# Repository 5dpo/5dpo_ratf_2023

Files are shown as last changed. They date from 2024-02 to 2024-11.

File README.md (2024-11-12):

# 5dpo_ratf_2023

System framework for the Robot@Factory 4.0 competition
([info](https://www.festivalnacionalrobotica.pt/2023/robotfactory-4-0/),
[GitHub](https://github.com/P33a/RobotAtFactory/tree/main)) hosted at the
[Portuguese Robotics Open (FNR)](https://www.festivalnacionalrobotica.pt/).
This framework is the lastest version developed by the
[5dpo Robotics Team](https://5dpo.github.io/) and used in the 2023 edition of
the competition.
Furthermore, the robot is a four-wheeled omnidirectional platform also developed
in the scope of the competition. All the information about the electrical and
mechanical components can be found below.
Finally, the launch file system implemented is bsed on the
[INESC TEC](https://www.inesctec.pt/en) Robotics Navigation Stack that allows
you to have different configurations implemented and selecting just one based on
your environment variables.

## Hardware

- Mechanics (3D files to print are available in [cad](/cad/)):
  - 60mm Aluminum Mecanum Wheels Set (2x left + 2x right, 45° rotational axis)
    ([shop](https://eu.robotshop.com/products/60mm-mecanum-wheel-set-2x-left-2x-right))
  - Metal DC Geared Motor w/Encoder - 12V 251RPM 18Kg.cm (DFRobot)
    ([shop-1](https://eu.robotshop.com/products/12v-dc-motor-251rpm-encoder),
    [shop-2](https://www.dfrobot.com/product-634.html))
- Computing Units:
  - Arduino Mega 2560 Rev3
    ([shop](https://store.arduino.cc/products/arduino-mega-2560-rev3))
  - Raspberry Pi 4B 4GB
    ([shop-1](https://mauser.pt/catalog/product_info.php?products_id=096-7402),
    [shop-2](https://pt.farnell.com/raspberry-pi/rpi4-modbp-4gb/raspberry-pi-4-model-b-4gb/dp/3051887),
    [shop-3](https://pt.mouser.com/ProductDetail/Raspberry-Pi/SC01949?qs=T%252BzbugeAwjjISb%252BwlagpRw%3D%3D),
    [shop-4](https://www.digikey.pt/en/products/detail/raspberry-pi/SC0194-9/10258781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))
- Electronics:
  - DC-DC Buck Converter 300W 6-40V to 1.2-36V 20A Step Dowm
    ([shop](https://www.amazon.com/DIANN-300W-DC-DC-Buck-Converter/dp/B0B4CZ6GRV))
  - Grove Electromagnet
    ([shop](https://eu.robotshop.com/products/grove-electromagnet))
  - LiPo Battery 11.1V 3S
    - Gens ace 5000mAh 11.1V 3S1P 60C Lipo Battery Pack with XT90 Plug Bashing
      Series
      ([shop](https://www.gensace.de/gens-ace-5000mah-11-1v-3s1p-60c-lipo-battery-pack-with-xt-90-plug-bashing-series.html))
    - Tattu 11.1V 15C 3S 10000mAh Lipo Battery Pack
      ([shop](https://www.gensace.de/tattu-11-1v-15c-3s-10000mah-lipo-battery-pack.html))
  - Micro Switch with Roller Lever Arm
    ([shop](https://mauser.pt/catalog/product_info.php?products_id=010-1473))
  - Power ON/OFF Switch
    ([shop](https://mauser.pt/catalog/product_info.php?products_id=010-0626))
- Sensors:
  - 10 DoF Inertial Measurement Unit (IMU)
    ([shop](https://www.waveshare.com/10-dof-imu-sensor-b.htm))
  - Raspberry Pi Camera Board v2.1 (8MP, 1080p)
    ([shop-1](https://mauser.pt/catalog/product_info.php?products_id=096-4061),
    [shop-2](https://pt.farnell.com/raspberry-pi/rpi-8mp-camera-board/raspberry-pi-camera-board-v2/dp/2510728),
    [shop-3](https://pt.mouser.com/ProductDetail/Raspberry-Pi/SC0023?qs=T%252BzbugeAwjgRU4vb4%252BbLIg%3D%3D),
    [shop-4](https://www.digikey.pt/en/products/detail/raspberry-pi/SC0023/6152810?s=N4IgTCBcDaIIwDYCcAGAtHFc5oHIBEQBdAXyA))
  - YDLIDAR X4 360° Laser Scanner
    ([shop](https://eu.robotshop.com/products/ydlidar-x4-360-laser-scanner))

## Firmware

- Arduino Mega 2560 Rev3 ([doc](https://docs.arduino.cc/hardware/mega-2560/))
- PlatformIO ([url](https://platformio.org/),
  [vscode](https://marketplace.visualstudio.com/items?itemName=platformio.platformio-ide),
  [clion](https://plugins.jetbrains.com/plugin/13922-platformio-for-clion))
  - Pre-requisite:
    ```sh
    sudo apt install python3-venv
    ```
  - Setup udev rules
    ([source](https://docs.platformio.org/en/stable/core/installation/udev-rules.html)):
    ```sh
    curl -fsSL https://raw.githubusercontent.com/platformio/platformio-core/develop/platformio/assets/system/99-platformio-udev.rules | sudo tee /etc/udev/rules.d/99-platformio-udev.rules

    sudo service udev restart
    sudo usermod -a -G dialout $USER
    sudo usermod -a -G plugdev $USER
    ```
  - If you want to define a fixed name to the serial port connection, add the
    following lines to a file `/etc/udev/rules.d/99-usb-serial.rule`
    ([source](https://roboticsknowledgebase.com/wiki/tools/udev-rules/)):
    ```conf
    SUBSYSTEM=="tty", ATTRS{idVendor}=="2341", ATTRS{idProduct}=="0042", SYMLINK+="ttyArduinoMega"
    ```
    - _Note:_ this approach creates a symbolic link, but the original device
      still appears in the `/dev/` folder
- Implementation: [5dpo_ratf_firmware](/firmware/5dpo_ratf_firmware/)

## ROS

**Current version**
- [Ubuntu 20.04.5 LTS](https://releases.ubuntu.com/focal/)
- [ROS Noetic](https://wiki.ros.org/noetic)

**Nodes**
- Drivers:
  - [sdpo_ratf_ros_driver](/drivers/5dpo_ratf_ros_driver/) (driver to
    communicate to the firmware running in the Arduino Mega 2560)
  - [sdpo_driver_omnijoy](/drivers/5dpo_driver_omnijoy/) (joystick driver
    compatible with omnidirectional platforms)
  - [sdpo_driver_laser_2d](/drivers/5dpo_driver_laser_2d/) (driver to
    communicate through a serial connection with the YDLIDAR X4)
  - [sdpo_driver_ros_camera](/drivers/5dpo_driver_ros_camera/) (camera driver
    to publish the poses of ArUco markers) _(NOT STABLE!)_
- Localization:
  - [sdpo_ros_odom](/localization/5dpo_ros_odom/) (wheeled odometry relative
    pose estimation)
  - [sdpo_ratf_ros_localization](/localization/5dpo_ratf_ros_localization/)
    (beacon-based Extended Kalman Filter to estimate the pose of the robot)
- Navigation:
  - [sdpo_ratf_ros_path_planning](/navigation/5dpo_ratf_ros_path_planning/)
    (trajectory controller and path planning to execute the competition rounds)
- Navigation Configuration:
  - [sdpo_ratf_ros_nav_conf](/5dpo_ratf_ros_nav_conf/) (launch file system)

## Usage

### Configurations

- `basic`
  - Drivers
    - [sdpo_ratf_ros_driver](/drivers/5dpo_ratf_ros_driver/)
    - [sdpo_driver_omnijoy](/drivers/5dpo_driver_omnijoy/)
  - Human-Machine Interface (HMI)
    - rviz
  - Localization
    - [sdpo_ros_odom](/localization/5dpo_ros_odom/)
- `ratf2023`
  - Drivers
    - [sdpo_ratf_ros_driver](/drivers/5dpo_ratf_ros_driver/)
    - [sdpo_driver_omnijoy](/drivers/5dpo_driver_omnijoy/)
    - [sdpo_driver_laser_2d](/drivers/5dpo_driver_laser_2d/)
  - Human-Machine Interface (HMI)
    - rviz
  - Localization
    - [sdpo_ros_odom](/localization/5dpo_ros_odom/)
    - [sdpo_ratf_ros_localization](/localization/5dpo_ratf_ros_localization/)
  - Navigation
    - [sdpo_ratf_ros_path_planning](/navigation/5dpo_ratf_ros_path_planning/)
- `ratf2023_imu_test` **(specific to Raspberry Pi!)**
  - Drivers
    - [imu_filter_madgwick](/drivers/imu_tools/imu_filter_madgwick/)
    - [MPU9255_node](/drivers/MPU9255_for_5dpo/)
    - [sdpo_ratf_ros_driver](/drivers/5dpo_ratf_ros_driver/)
    - [sdpo_driver_omnijoy](/drivers/5dpo_driver_omnijoy/)
    - [sdpo_driver_laser_2d](/drivers/5dpo_driver_laser_2d/)
  - Human-Machine Interface (HMI)
    - rviz
  - Localization
    - [robot_pose_ekf](/localization/robot_pose_ekf/)
    - [sdpo_ros_odom](/localization/5dpo_ros_odom/)
    - [sdpo_ratf_ros_localization](/localization/5dpo_ratf_ros_localization/)
  - Navigation
    - [sdpo_ratf_ros_path_planning](/navigation/5dpo_ratf_ros_path_planning/)
  - You may need to either clone the source of additional dependencies or
    installing the following nodes:
    ```sh
    sudo apt install ros-noetic-robot-pose-ekf
    sudo apt install ros-noetic-imu-complementary-filter
    ```
    - **Note:** if you do not want to use the IMU, please add a `CATKIN_IGNORE`
      file inside each of the IMU-specific nodes. Also, given that the MPU node
      requires a specific library of Raspberry Pi for communication with the
      IMU, the code will not compile in your x86 system.

**Usage**

```sh
# Robot id
export ROBOT_ID=<id>                # (default: unnamed_robot)
# Configuration
export ROBOT_CONF=<configuration>   # (default: basic)
```

If you want to set up a persistent `ROBOT_ID` environment variable, add the
following line to the file `/etc/environment`:

```sh
ROBOT_ID=<id>
```

### Build

```sh
mkdir ~/ros1_ws/src -p
cd ~/ros1_ws/src

git clone git@github.com:5dpo/5dpo_ratf_2023.git

cd ../
catkin_make --force-cmake -DCMAKE_BUILD_TYPE=Release
```

### Launch

```sh
export ROBOT_CONF=<basic|ratf2023>
roslaunch sdpo_ratf_ros_nav_conf wake_up_almighty_ratf.launch
```

## License

Distributed under the _MIT License_.
See [LICENSE](/LICENSE) for more information.

## References
If using this code for research purposes, please cite:
```bash
@INPROCEEDINGS{5dpoRAF,
  author={Sousa, Ricardo B. and Rocha, Cláudia D. and Martins, João G. and Pedro Costa, João and Padrão, João Tomás and Sarmento, José Maria and Carvalho, José Pedro and Lopes, Maria S. and Costa, Paulo G. and Moreira, António Paulo},
  booktitle={2024 IEEE International Conference on Autonomous Robot Systems and Competitions (ICARSC)}, 
  title={A Robotic Framework for the Robot@Factory 4.0 Competition}, 
  year={2024},
  volume={},
  number={},
  pages={66-73},
  doi={10.1109/ICARSC61747.2024.10535935}}
```

## Contacts

- António Paulo Moreira ([github](https://github.com/apaulomoreira),
  [mail](mailto:amoreira@fe.up.pt))
- Cláudia Daniela Rocha ([github](https://github.com/rochaclaudia),
  [mail](mailto:claudia.d.rocha@inesctec.pt))
- João G. Martins ([github](https://github.com/Joao-G-Martins),
  [mail:student](mailto:up201806222@edu.fe.up.pt),
  [mail:inesctec](mailto:joao.g.martins@inesctec.pt))
- João Pedro Costa ([github](https://github.com/costajoao1641),
  [mail](mailto:up201806431@edu.fe.up.pt))
- João Tomás Padrão ([github](https://github.com/JoaoP4dr4o),
  [mail](mailto:up202108766@edu.fe.up.pt))
- José Maria Sarmento ([github](https://github.com/JoseMQS),
  [mail](mailto:jose.m.sarmento@inesctec.pt))
- José Pedro Carvalho ([github](https://github.com/Jose-PCarvalho),
  [mail](mailto:jpcarvalho@fe.up.pt))
- Maria Silva Lopes ([github](https://github.com/mariaslopes),
  [mail:student](mailto:up201806775@edu.fe.up.pt),
  [mail:inesctec](mailto:maria.s.lopes@inesctec.pt))
- Paulo José Gomes da Costa ([github](https://github.com/P33a),
  [mail](mailto:paco@fe.up.pt))
- Ricardo B. Sousa ([github](https://github.com/sousarbarb/),
  [gitlab](https://gitlab.inesctec.pt/ricardo.b.sousa),
  [mail:inesctec](mailto:ricardo.b.sousa@inesctec.pt),
  [mail:personal](mailto:sousa.ricardob@outlook.com),
  [mail:student](mailto:up201503004@edu.fe.up.pt))

Project Link:
https://github.com/5dpo/5dpo_ratf_2023/.

## Acknowledgements

- [Faculty of Engineering, University of Porto (FEUP)](https://sigarra.up.pt/feup/en/)
- [Electrical and Computers Engineering Department (DEEC) @ FEUP](https://sigarra.up.pt/feup/en/UNI_GERAL.UNIDADE_VIEW?pv_unidade=13)
- [CRIIS - Centre for Robotics in Industry and Intelligent Systems](https://www.inesctec.pt/en/centres/criis/) from
  [INESC TEC - Institute for Systems and Computer Engineering, Technology and Science](https://www.inesctec.pt/en/)

## Funding

TBC.

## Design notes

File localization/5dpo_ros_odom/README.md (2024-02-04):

# [5dpo_ros_odom](https://github.com/5dpo/5dpo_ros_odom)

This repository implements a data processor for the estimation of the robot pose
based on odometric-only data (e.g., wheeled, laser, visual, and/or inertial
odometry). The ROS package implemented in this repository makes available nodes
that may leverage one and/or multiple sources of odometry data for dead
reckoning pose estimation of the robot.

**Version 1.4.0**

**With this version, it is possible to do:**

- Wheeled odometry (four-wheeled omnidirectional steering geometry)
- Wheeled odometry (differential and three-wheeled omnidirectional steering
  geometries)
- Inverse wheeled odometry
- Enable/disable publication of the tf base_frame_id > odom_frame_id
- Limit the maximum angular speed of the wheels and scale the velocities

**The next version will add these features:**

- Wheeled odometry (tricycle steering geometry)
- Fusion of wheels and inertial odometry data

## ROS

**Current version:**

- [Ubuntu 20.04.5 LTS](https://releases.ubuntu.com/focal/)
- [ROS Noetic](https://wiki.ros.org/noetic)

### Dependencies

- [roscpp](https://wiki.ros.org/roscpp)
- [geometry_msgs](https://wiki.ros.org/geometry_msgs)
- [nav_msgs](https://wiki.ros.org/nav_msgs)
- [sdpo_ros_interfaces_hw](https://github.com/5dpo/5dpo_ros_interfaces)
- [tf](https://wiki.ros.org/tf)

### Parameters

- base_frame_id (`std::string = "base_footprint"`): tf frame id of the robot
  base footprint coordinate frame
- odom_frame_id (`std::string = "odom"`): tf frame id of the robot odometry
  coordinate frame
- publish_tf (`bool = true`): enable the publication of the tf
  base_frame_id > odom_frame_id
- steering_geometry: steering geometry of the mobile robot
  (`"diff" | "tricyc" | "omni3" | "omni4"`)
  - w_ref_max_enabled (`bool = false`): enable a maximum angular speed for the
    robot wheels
  - w_ref_max (`double`): maximum angular speed of the robot wheels
  - Differential drive
    - rob_dist_between_wh (`double`): distance between left-right wheels (m)
    - wh_right_diam (`double`): right wheel diameter (m)
    - wh_right_idx (`size_t`): right wheel index in the
      [mot_enc_array.msg](https://github.com/5dpo/5dpo_ros_interfaces/blob/main/5dpo_ros_interfaces_hw/msg/mot_enc_array.msg)
      (0..1)
    - wh_right_inv (`bool`): invert positive direction of the right
      wheel angular motion
    - wh_left_diam (`double`): left wheel diameter (m)
    - wh_left_idx (`size_t`): left wheel index in the
      [mot_enc_array.msg](https://github.com/5dpo/5dpo_ros_interfaces/blob/main/5dpo_ros_interfaces_hw/msg/mot_enc_array.msg)
      (0..1)
    - wh_left_inv (`bool`): invert positive direction of the left
      wheel angular motion
  - Tricycle
    - TBD 
  - Three-wheeled omnidirectional robot
    - rob_dist_center_wh (`double`): distance between the robot geometric center
      and the omnidirectional wheels (m)
    - wh_front_right_diam (`double`): front-right wheel diameter (m)
    - wh_front_right_idx (`size_t`): front-right wheel index in the
      [mot_enc_array.msg](https://github.com/5dpo/5dpo_ros_interfaces/blob/main/5dpo_ros_interfaces_hw/msg/mot_enc_array.msg)
      (0..2)
    - wh_front_right_inv (`bool`): invert positive direction of the front-right
      wheel angular motion
    - wh_front_left_diam (`double`): front-left wheel diameter (m)
    - wh_front_left_idx (`size_t`): front-left wheel index in the
      [mot_enc_array.msg](https://github.com/5dpo/5dpo_ros_interfaces/blob/main/5dpo_ros_interfaces_hw/msg/mot_enc_array.msg)
      (0..2)
    - wh_front_left_inv (`bool`): invert positive direction of the front-left
      wheel angular motion
    - wh_back_diam (`double`): back wheel diameter (m)
    - wh_back_idx (`size_t`): back wheel index in the
      [mot_enc_array.msg](https://github.com/5dpo/5dpo_ros_interfaces/blob/main/5dpo_ros_interfaces_hw/msg/mot_enc_array.msg)
      (0..2)
    - wh_back_inv (`bool`): invert positive direction of the back
      wheel angular motion
  - Four-wheeled omnidirectional robot
    - rob_dist_between_front_back_wh (`double`): distance between front-back
      wheels (m)
    - rob_dist_between_left_right_wh (`double`): distance between left-right
      wheels (m)
    - wh_front_left_diam (`double`): front-left wheel diameter (m)
    - wh_front_left_idx (`size_t`): front-left wheel index in the
      [mot_enc_array.msg](https://github.com/5dpo/5dpo_ros_interfaces/blob/main/5dpo_ros_interfaces_hw/msg/mot_enc_array.msg)
      (0..3)
    - wh_front_left_inv (`bool`): invert positive direction of the front-left
      wheel angular motion
    - wh_front_right_diam (`double`): front-right wheel diameter (m)
    - wh_front_right_idx (`size_t`): front-right wheel index in the
      [mot_enc_array.msg](https://github.com/5dpo/5dpo_ros_interfaces/blob/main/5dpo_ros_interfaces_hw/msg/mot_enc_array.msg)
      (0..3)
    - wh_front_right_inv (`bool`): invert positive direction of the front-right
      wheel angular motion
    - wh_back_left_diam (`double`): back-left wheel diameter (m)
    - wh_back_left_idx (`size_t`): back-left wheel index in the
      [mot_enc_array.msg](https://github.com/5dpo/5dpo_ros_interfaces/blob/main/5dpo_ros_interfaces_hw/msg/mot_enc_array.msg)
      (0..3)
    - wh_back_left_inv (`bool`): invert positive direction of the back-left
      wheel angular motion
    - wh_back_right_diam (`double`): back-right wheel diameter (m)
    - wh_back_right_idx (`size_t`): back-right wheel index in the
      [mot_enc_array.msg](https://github.com/5dpo/5dpo_ros_interfaces/blob/main/5dpo_ros_interfaces_hw/msg/mot_enc_array.msg)
      (0..3)
    - wh_back_right_inv (`bool`): invert positive direction of the back-right
      wheel angular motion

### Subscribes

- cmd_vel
  ([Twist.msg](https://docs.ros.org/en/noetic/api/geometry_msgs/html/msg/Twist.html))

**sdpo_ros_odom_wh**

- motors_encoders
  ([mot_enc_array.msg](https://github.com/5dpo/5dpo_ros_interfaces/blob/main/5dpo_ros_interfaces_hw/msg/mot_enc_array.msg))

### Publishes

- cmd_vel_ref
  ([Twist.msg](https://docs.ros.org/en/noetic/api/geometry_msgs/html/msg/Twist.html))
- motors_ref
  ([mot_ref.msg](https://github.com/5dpo/5dpo_ros_interfaces/blob/main/5dpo_ros_interfaces_hw/msg/mot_ref.msg))
- odom
  ([Odometry.msg](https://docs.ros.org/en/noetic/api/nav_msgs/html/msg/Odometry.html))
- tf (N/A)
  - base_frame_id > odom_frame_id

### Services

None.

### Actions

None.

## Usage

### Build

```sh
# Create catkin workspace
mkdir -p ~/catkin_ws/src

# Clone repository
cd ~/catkin_ws/src
git clone git@github.com:5dpo/5dpo_ros_odom.git

# Build
cd ..
catkin build
# OR catkin_make_isolated (more slow, build and check dependencies individually)
# OR catkin build (requires catkin tools)
```

### Launch

**sdpo_ros_odom_wh**

```sh
roslaunch sdpo_ros_odom sdpo_ros_odom_wh.launch
```

## Contacts

If you have any questions or you want to know more about this work, please
contact one of the contributors of this package:

- Héber Miguel Sobreira ([github](https://github.com/HeberSobreira),
  [gitlab](https://gitlab.inesctec.pt/heber.m.sobreira),
  [mail](mailto:heber.m.sobreira@inesctec.pt))
- Ricardo B. Sousa ([github](https://github.com/sousarbarb/),
  [gitlab](https://gitlab.inesctec.pt/ricardo.b.sousa),
  [mail:inesctec](mailto:ricardo.b.sousa@inesctec.pt),
  [mail:personal](mailto:sousa.ricardob@outlook.com),
  [mail:professor](mailto:rbs@fe.up.pt),
  [mail:student](mailto:up201503004@edu.fe.up.pt))

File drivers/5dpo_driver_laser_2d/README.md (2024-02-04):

# [5dpo_driver_laser_2d](https://github.com/5dpo/5dpo_driver_laser_2d)

This repository focus on developing a driver for communicating with
[RPLIDAR](https://www.slamtec.com/en) and variants (specifically,
[YDLIDAR](https://www.ydlidar.com/)) of 2D laser scanners.
The main purpose is to be able to compensate in the future the linear and
angular velocity in the laser data.

**Version 2.4.0**

**With this version, it is possible to do:**

- [YDLIDAR X4](https://www.ydlidar.com/products/view/5.html) support
- [RPLIDAR S2](https://www.slamtec.com/en/S2) support
- tf publication of the laser pose relative to the robot's coordinate frame
- Library available to use the lasers outside of this ROS package
- Dynamic reconfiguration of the laser pose relative to the base footprint
  coordinate frame

**The next version will add these features:**

- [RPLIDAR S2](https://www.slamtec.com/en/S2) dense mode

## ROS

**Current version:**

- [Ubuntu 20.04.5 LTS](https://releases.ubuntu.com/focal/)
- [ROS Noetic](https://wiki.ros.org/noetic)

### Dependencies

- [roscpp](https://wiki.ros.org/roscpp)
- [rospy](https://wiki.ros.org/rospy)
- [dynamic_reconfigure](https://wiki.ros.org/dynamic_reconfigure)
- [sdpo_ros_serial_port](https://github.com/5dpo/5dpo_ros_serial_port)
- [sensor_msgs](https://wiki.ros.org/sensor_msgs)
- [tf](https://wiki.ros.org/tf)

### Parameters

- model (`std::string`): model of the 2D laser (`"rplidars2" | "ydlidarx4"`)
- serial_port_name (`std::string = "/dev/ttyUSB0"`): name of the serial port
  - **Note:** do not forget to execute the following commands in the terminal:
    ```shell
    # Add user to group
    sudo usermod -a -G dialout $USER
    sudo usermod -a -G plugdev $USER

    # Update permissions of the serial port (a - all users + rw - read&write)
    sudo chmod a+rw /dev/ttyUSB0
    ```
- baud_rate (`unsigned int`): baud rate of the serial connection (bps)
  - [YDLIDAR X4](https://www.ydlidar.com/products/view/5.html): `115200`
  - [RPLIDAR S2](https://www.slamtec.com/en/S2): `1000000`
- base_frame_id (`std::string = "base_footprint"`): tf frame id of the robot
  base footprint coordinate frame
- laser_frame_id (`std::string = "laser"`): tf frame id of the 2D laser scanner
  coordinate frame
- laser_pose_x (`float = 0.0`): x of the laser pose relative to the robot base
  footprint coordinate frame (m)
- laser_pose_y (`float = 0.0`): y of the laser pose relative to the robot base
  footprint coordinate frame (m)
- laser_pose_z (`float = 0.0`): z of the laser pose relative to the robot base
  footprint coordinate frame (m)
- laser_pose_yaw (`float = 0.0`): yaw angle of the laser pose relative to the
  robot base footprint coordinate frame (deg)
- laser_pose_pitch (`float = 0.0`): pitch angle of the laser pose relative to
  the robot base footprint coordinate frame (deg)
- laser_pose_roll (`float = 0.0`): roll angle of the laser pose relative to the
  robot base footprint coordinate frame (deg)
- dist_min (`float`): minimum distance range (m)
- dist_max (`float`): maximum distance range (m)
- angle_min (`float`): minimum angle range (deg, `[-180.0, 180.0[`)
- angle_max (`float`): maximum angle range (deg, `[-180.0, 180.0[`)
  - **Note:** if a minimum or a maximum value is set, both limits must be
    defined!

### Subscribes

None.

### Publishes

- laser_scan_point_cloud
  ([PointCloud.msg](https://docs.ros.org/en/api/sensor_msgs/html/msg/PointCloud.html))
- tf (N/A)
  - laser_frame_id > base_frame_id

### Services

None.

### Actions

None.

## Usage

### Build

```sh
# Create catkin workspace
mkdir -p ~/catkin_ws/src

# Clone repository
cd ~/catkin_ws/src
git clone git@github.com:5dpo/5dpo_driver_laser_2d.git

# Build
cd ..
catkin build
# OR catkin_make_isolated (more slow, build and check dependencies individually)
# OR catkin build (requires catkin tools)
```

### Launch

**[YDLIDAR X4](https://www.ydlidar.com/products/view/5.html)**

```sh
roslaunch sdpo_driver_laser_2d sdpo_driver_laser_2d_YDLIDARX4.launch
```

**[RPLIDAR S2](https://www.slamtec.com/en/S2)**

```sh
roslaunch sdpo_driver_laser_2d sdpo_driver_laser_2d_RPLIDARS2.launch
```

## Contacts

If you have any questions or you want to know more about this work, please
contact one of the contributors of this package:

- Héber Miguel Sobreira ([github](https://github.com/HeberSobreira),
  [gitlab](https://gitlab.inesctec.pt/heber.m.sobreira),
  [mail](mailto:heber.m.sobreira@inesctec.pt))
- Ricardo B. Sousa ([github](https://github.com/sousarbarb/),
  [gitlab](https://gitlab.inesctec.pt/ricardo.b.sousa),
  [mail:inesctec](mailto:ricardo.b.sousa@inesctec.pt),
  [mail:personal](mailto:sousa.ricardob@outlook.com),
  [mail:professor](mailto:rbs@fe.up.pt),
  [mail:student](mailto:up201503004@edu.fe.up.pt))

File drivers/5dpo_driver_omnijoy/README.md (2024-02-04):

# 5dpo_driver_omnijoy

**Version 0.0.0**

This repository implements a ROS driver to control an omnidirectional robot
(but also compatible with other steering geometries) with a joystick controller.

**With this version, it is possible to do:**

- Joystick control of a mobile robot

**The next version will add these features:**

- No further development is foreseen for this package

## ROS

**Current version:**

- [Ubuntu 20.04.5 LTS](https://releases.ubuntu.com/focal/)
- [ROS Noetic](https://wiki.ros.org/noetic)

### Dependencies

- [roscpp](https://wiki.ros.org/roscpp)
- [geometry_msgs](https://wiki.ros.org/geometry_msgs)
- [joy](https://wiki.ros.org/joy)

### Parameters

- axis_linear_x (`int = 1`): index number of x linear axis (`/joy.axes`)
- axis_linear_y (`int = 2`): index number of y linear axis (`/joy.axes`)
- axis_angular (`int = 0`): index number of angular linear axis (`/joy.axes`)
- axis_deadman (`int = 4`): index number of button for deadman switch
  (`/joy.buttons`)
- axis_turbo (`int = 5`): index number of button for turbo (`/joy.buttons`)
- axis_turbo_up (`int = 6`): index number of button for increasing boost
  (`/joy.buttons`)
- axis_turbo_down (`int = 7`): index number of button for decreasing boost
  (`/joy.buttons`)
- scale_angular (`double = 0.2`): angular scale to normalize
  [`Joy.msg`](https://docs.ros.org/en/melodic/api/sensor_msgs/html/msg/Joy.html)
- scale_linear (`double = 0.1`): linear scale to normalize
  [`Joy.msg`](https://docs.ros.org/en/melodic/api/sensor_msgs/html/msg/Joy.html)
- turbo_scale_linear (`double = 0.2`): use this scale instead of `scale_linear`
  when pressing the turbo button
- turbo_max_scale_linear (`double = 0.4`): maximum turbo scale
- turbo_scale_angular (`double = 0.4`): use this scale instead of
  `scale_angular` when pressing the turbo button

In order to know the index numbers of your controller, go to
[joy](https://wiki.ros.org/joy) documentation, _5. Application_, to see the
options available for those parameters.

### Subscribes

- joy
([`Joy.msg`](https://docs.ros.org/en/melodic/api/sensor_msgs/html/msg/Joy.html))

### Publishes

- cmd_vel
  ([`Twist.msg`](https://docs.ros.org/en/noetic/api/geometry_msgs/html/msg/Twist.html))

### Services

None.

### Actions

None.

## Usage

### Build

```sh
# Create catkin workspace
mkdir -p ~/catkin_ws/src

# Clone repository
cd ~/catkin_ws/src
git clone git@github.com:5dpo/5dpo_driver_omnijoy.git

# Build
cd ..
catkin build
```

### Launch

```sh
roslaunch sdpo_driver_omnijoy sdpo_driver_omnijoy.launch
```

## Contacts

If you have any questions or you want to know more about this work, please
contact one of the contributors of this package:

- Fernando Sá ([gitlab](https://gitlab.inesctec.pt/fjms))
- Héber Miguel Sobreira ([gitlab](https://gitlab.inesctec.pt/heber.m.sobreira),
  [inesctec](mailto:heber.m.sobreira@inesctec.pt))
- Ricardo B. Sousa ([github](https://github.com/sousarbarb/),
  [gitlab](https://gitlab.com/sousarbarb/),
  [personal](mailto:sousa.ricardob@outlook.com),
  [feup:professor](mailto:rbs@fe.up.pt),
  [feup:student](mailto:up201503004@edu.fe.up.pt),
  [inesctec](mailto:ricardo.b.sousa@inesctec.pt))

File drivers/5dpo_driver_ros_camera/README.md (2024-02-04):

# [5dpo_driver_ros_camera](https://github.com/5dpo/5dpo_driver_ros_camera)

This package contains the camera driver with Aruco pose estimation designed for
use in the 2023 5DPO Robot@Factory robots.

**Version 0.0.0**

**With this version, it is possible to do:**

- TBC

**The next version will add these features:**

- TBC

## ROS

**Current version:**

- [Ubuntu 20.04.5 LTS](https://releases.ubuntu.com/focal/)
- [ROS Noetic](https://wiki.ros.org/noetic)

### Dependencies

- [roscpp](https://wiki.ros.org/roscpp)
- [dynamic_reconfigure](https://wiki.ros.org/dynamic_reconfigure)
- [geometry_msgs](https://wiki.ros.org/geometry_msgs)
- [message_generation](https://wiki.ros.org/message_generation)
- [message_runtime](https://wiki.ros.org/message_runtime)
- [roslib](https://wiki.ros.org/roslib)
- [std_msgs](https://wiki.ros.org/std_msgs)
- [tf](https://wiki.ros.org/tf)

### Parameters

To obtain the camera's intrinsic parameters, please refer to the following
tutorial:
[OpenCV Camera Calibration](https://docs.opencv.org/4.x/d4/d94/tutorial_camera_calibration.html). Place the generated file in the
[config](config/) folder and ensure the proper file name is placed in the launch
file.

- debug (`bool = false`): enable/disable additional messages and showing the
  camera image
- publish_rate (`int = 20`): publication rate of the arucos perceived by the
  camera (Hz)
- base_frame_id (`string = "base_footprint"`): tf frame id of the robot base
  footprint coordinate frame
- camera_frame_id (`string = "camera"`): tf frame id of the camera coordinate
  frame
- camera_pose_x (`float = 0.0`): x of the camera pose relative to the robot base
  footprint coordinate frame (m)
- camera_pose_y (`float = 0.0`): y of the camera pose relative to the robot base
  footprint coordinate frame (m)
- camera_pose_z (`float = 0.0`): z of the camera pose relative to the robot base
  footprint coordinate frame (m)
- camera_pose_yaw (`float = 0.0`): yaw angle of the camera pose relative to the
  robot base footprint coordinate frame (deg)
- camera_pose_pitch (`float = 0.0`): pitch angle of the camera pose relative to
  the robot base footprint coordinate frame (deg)
- camera_pose_roll (`float = 0.0`): roll angle of the camera pose relative to
  the robot base footprint coordinate frame (deg)

### Subscribes

None.

### Publishes

- arucos
  ([sdpo_driver_ros_camera/ArucoArray.msg](msg/ArucoArray.msg))
- tf (N/A)
  - camera_frame_id > base_frame_id

### Services

None.

### Actions

None.

## Usage

### Build

```sh
# Create catkin workspace
mkdir -p ~/catkin_ws/src

# Clone repository
cd ~/catkin_ws/src
git clone git@github.com:5dpo/5dpo_driver_ros_camera.git

# Build
cd ..
catkin build
# OR catkin_make_isolated (more slow, build and check dependencies individually)
# OR catkin build (requires catkin tools)
```

### Launch

TBC

## Contacts

If you have any questions or you want to know more about this work, please
contact one of the contributors of this package:

- João Costa ([github](https://github.com/costajoao1641/),
  [mail:student](mailto:up201806431@fe.up.pt))
- Ricardo B. Sousa ([github](https://github.com/sousarbarb/),
  [gitlab](https://gitlab.inesctec.pt/ricardo.b.sousa),
  [mail:inesctec](mailto:ricardo.b.sousa@inesctec.pt),
  [mail:personal](mailto:sousa.ricardob@outlook.com),
  [mail:professor](mailto:rbs@fe.up.pt),
  [mail:student](mailto:up201503004@edu.fe.up.pt))
- Vítor Ventuzelos ([github](https://github.com/BerserkingIdiot),
  [gitlab](https://gitlab.inesctec.pt/vitor.ventuzelos),
  [mail:inesctec](mailto:vitor.ventuzelos@inesctec.pt),
  [mail:personal](mailto:skullventuzelos@hotmail.com))

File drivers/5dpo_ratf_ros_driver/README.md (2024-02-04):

# [5dpo_ratf_ros_driver](https://github.com/5dpo/5dpo_ratf_ros_driver)

This repository implements a driver within a ROS package to communicate with the
firmware present in the four-wheeled omnidirectional robotic platform used by
the [5dpo FEUP Robotics Team](https://github.com/5dpo) in the
[Robot@Factory](https://www.festivalnacionalrobotica.pt/) competition. The
driver is required for communicating with the robot and have available all its
different functions.

The serial communication is handled by
[Boost.Asio](https://www.boost.org/doc/libs/1_80_0/doc/html/boost_asio.html).
This communication is based on the example `4_callback` provided in the
[serial-port](https://github.com/fedetft/serial-port) GitHub repository.

**Version 1.4.0**

**With this version, it is possible to do:**

- Communicate with Arduino Mega 2560 using Boost.Asio
  ([sdpo_ros_serial_port](https://github.com/5dpo/5dpo_ros_serial_port))
- Subscribe motors angular speed reference
- Publish encoders data (encoders + wheels angular speed)
- Read encoders
- Set motors speed
- Reset driver upon reset signal
- Watchdog timer to monitor the motors angular speed reference
- Send serial message to the firmware upon reconnection of the serial port
  communication
- Read switch
- Set solenoid
- Node specific for setting PWM values through ROS services and log data for
  future calibration of the PI controllers
- Scripts (see in [sh](sh/)) to automate the retrieval of log data for tunning
  the PI controllers
- Synchronization of the firmware with the ROS publication topics

**The next version will add these features:**

- Publish optionally the odometry data

## ROS

**Current version:**

- [Ubuntu 20.04.5 LTS](https://releases.ubuntu.com/focal/)
- [ROS Noetic](https://wiki.ros.org/noetic)

### Dependencies

- [roscpp](https://wiki.ros.org/roscpp)
- [message_generation](https://wiki.ros.org/message_generation)
- [message_runtime](https://wiki.ros.org/message_runtime)
- [sdpo_ros_interfaces_hw](https://github.com/5dpo/5dpo_ros_interfaces)
- [sdpo_ros_serial_port](https://github.com/5dpo/5dpo_ros_serial_port)
- [serial_communication_channels](https://github.com/5dpo/serial_communication_channels)
- [std_msgs](https://wiki.ros.org/std_msgs)
- [std_srvs](https://wiki.ros.org/std_srvs)

### Parameters

- enc_ticks_per_rev (`float = 64.0`): resolution of the encoder (ticks/rot)
- gear_reduction (`float = 43.8`): reduction ratio of the transmissions
  (\[gear_reduction:1\])
- serial_port_name (`std::string = "/dev/ttyACM0"`): name of the serial port

### Subscribes

- motors_ref
  ([mot_ref.msg](https://github.com/5dpo/5dpo_ros_interfaces/blob/main/5dpo_ros_interfaces_hw/msg/mot_ref.msg))

### Publishes

- motors_encoders
  ([mot_enc_array.msg](https://github.com/5dpo/5dpo_ros_interfaces/blob/main/5dpo_ros_interfaces_hw/msg/mot_enc_array.msg))
- switch_state
  ([Bool.msg](https://docs.ros.org/en/api/std_msgs/html/msg/Bool.html))

**sdpo_ratf_ros_driver_tune**

- motors_data
  ([mot_data_array.msg](https://github.com/5dpo/5dpo_ros_interfaces/blob/main/5dpo_ros_interfaces_hw/msg/mot_data_array.msg))

### Services

- set_solenoid_state
  ([SetBool.srv](https://docs.ros.org/en/api/std_srvs/html/srv/SetBool.html))

**sdpo_ratf_ros_driver_tune**

- set_motors_pwm ([SetMotorsPWM.srv](srv/SetMotorsPWM.srv))
  ```sh
  rosservice call /unnamed_robot/set_motors_pwm [0,0,0,0]
  ```

### Actions

None.

## Usage

### Build

```sh
# Create catkin workspace
mkdir -p ~/catkin_ws/src

# Clone repository
cd ~/catkin_ws/src
git clone git@github.com:5dpo/5dpo_ratf_ros_driver.git

# Build
cd ..
catkin build
```

### Launch

**sdpo_ratf_ros_driver_node**

```sh
roslaunch sdpo_ratf_ros_driver sdpo_ratf_ros_driver.launch
```

**sdpo_ratf_ros_driver_tune**

1. Measure the battery level with a multimeter
2. Open a terminal and launch the node
   ```sh
   roslaunch sdpo_ratf_ros_driver sdpo_ratf_ros_driver_tune.launch battery:=<battery level>
   ```
3. Open another terminal and use the shell scripts provided in this repository
   - [set_robot_pwm.sh](sh/set_robot_pwm.sh)
     ```sh
     ./set_robot_pwm.sh <v,vn,w> <pwm value>
     ```
     - w / #ticks = f(PWM)
     - E.g., estimate the deadzone of the motor and tune the Hammerstein
       nonlinear block implemented in the firmware
   - [auto_tunning_motion.sh](sh/auto_tunning_motion.sh)
     ```sh
     ./auto_tunning_motion.sh <#runs per motion> <time per motion state (s)> <v,vn: pwm ini> <v,vn: pwm fin> <w: pwm ini> <w: pwm fin>
     ```
     - w / #ticks = f(PWM)
     - Shell script to automatically perform v, vn, w motions to use the logged
       data for tunning the PI controller with, e.g., the _Internal Model_
       _Control (IMC) method_

## Contacts

If you have any questions or you want to know more about this work, please
contact one of the contributors of this package:

- Héber Miguel Sobreira ([gitlab](https://gitlab.inesctec.pt/heber.m.sobreira),
  [inesctec](mailto:heber.m.sobreira@inesctec.pt))
- Ricardo B. Sousa ([github](https://github.com/sousarbarb/),
  [gitlab](https://gitlab.com/sousarbarb/),
  [personal](mailto:sousa.ricardob@outlook.com),
  [feup:professor](mailto:rbs@fe.up.pt),
  [feup:student](mailto:up201503004@edu.fe.up.pt),
  [inesctec](mailto:ricardo.b.sousa@inesctec.pt))

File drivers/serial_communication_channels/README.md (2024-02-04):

# serial_communication_channels

**Version 1.0**

This folder contains a ROS package that defines a library to communicate with
another devices such as Arduinos (Uno, Mega, etc). The communication protocol is
based on the _channels_ library developed by professor Paulo Costa. The current
version is an improvement over the one developed by Héber Sobreira
(https://gitlab.inesctec.pt/heber.m.sobreira/serial_communication_channels.git)
in the way that allows channels between 'g'-'z' and 'G'-'Z'. An important note
is that you must check if on the Arduino side the hexdecimals characters
correspond to the ones consider in this package: '0'..'9','A'..'F'.

Lastly, it is possible to use the same library on the Arduino (example provided
by Héber Sobreira - please contact him for further informations on this matter).
However, this implementation uses reallocs of memory. Even though it is only 
when the Arduino turns on, I did not think that this approach would be the
correct one due to Arduinos do not have a proper memory management system. So,
the one used on the Arduino is the same one developed by professor Paulo Costa.
**Main disadvantage:** the Arduino only interprets fixed-size packets
(specifically, 4 bytes of data: `float`, `uint32_t` or `int32_t`).

**With this version, it is possible to:**

- Send data of the following types: `float`, `uint32_t` or `int32_t`
  (limited because of the implementation on the Arduino side)
- 40 different channels with different functions associated with each one
  ('g'-'z' and 'G'-'Z')

**The next version will add these features:**

- It is not expected any further developments on this library

## Communication Protocol

- `[CHANNEL]` + `[DATA]` + `\0`
- `[CHANNEL]`: 'g'-'z', 'G'-'Z'
- `[DATA]`: characters that represent a value in hexadecimal

## Contacts

If you have any questions or you want to know more about this work, please contact one of the contributors of this package:

- Héber Miguel Sobreira ([gitlab](https://gitlab.inesctec.pt/heber.m.sobreira),
  [inesctec](mailto:heber.m.sobreira@inesctec.pt))
- Ricardo B. Sousa ([github](https://github.com/sousarbarb/),
  [gitlab](https://gitlab.com/sousarbarb/),
  [personal](mailto:sousa.ricardob@outlook.com),
  [feup:professor](mailto:rbs@fe.up.pt),
  [feup:student](mailto:up201503004@edu.fe.up.pt),
  [inesctec](mailto:ricardo.b.sousa@inesctec.pt))

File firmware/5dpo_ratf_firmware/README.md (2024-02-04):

# [5dpo_ratf_firmware](https://github.com/5dpo/5dpo_ratf_firmware)

This repository implements the firmware relative to the four-wheeled
omnidirectional robotic platform used by the
[5dpo FEUP Robotics Team](https://github.com/5dpo) in the 
[Robot@Factory](https://www.festivalnacionalrobotica.pt/) competition.

**Version 1.0.3**

**With this version, it is possible to do:**

- Serial communication using the library channels
- Read encoders channel A and B for wheeled odometry
- Motors angular speed control with a generic PID controller
- Motors PWM control using the Adafruit Motor Shield V2
- Watchdog timer to disable the motors if the PC does not send anything for a
  certain time
- Limitation on the PWM change
- Reset signal
- Solenoid actuator
- Switch to sense the presence of a box
- Tune the PID controllers for angular speed control of the motors
  (same parameters as the original version used in the competition)
- Fix control period of the motors (100Hz > 50Hz)
- Tune the PID controllers for angular speed control of the motors
- Switch off solenoid actuator when the motors are disabled due to watchdog
  timer

**The next version will add these features:**

No further development is expected for this module.

**Bugs identified in the current version:**

- TBC

## Hardware (TBC)

- 60mm Aluminum Mecanum Wheels Set
  (2x left + 2x right, 45° rotational axis)
- Adafruit Motor Shield V2
- Arduino Mega 2560 Rev3
- DC-DC Buck Converter 300W 6-40V to 1.2-36V 20A Step Dowm
- Grove Electromagnet
- Metal DC Geared Motor w/Encoder - 12V 251RPM 18Kg.cm (DFRobot)
- Raspberry Pi 4
- Raspberry Pi Camera Board v2.1 (8MP, 1080p)
- TATTU 10000mAh 11.1V 3S 15C LiPo Battery
- Waveshare 5inch Capacitive Touch Display (DSI Interface, 800×480)
- YDLIDAR X4 360° Laser Scanner

## Serial Communication (channels)

**Robot > PC**

- `[g]`: encoders total count of motor 0 (ticks)
- `[h]`: encoders total count of motor 1 (ticks)
- `[i]`: encoders total count of motor 2 (ticks)
- `[j]`: encoders total count of motor 3 (ticks)
- `[k]`: interval time between control cycles (us)
- `[r]`: reset signal
- `[s]`: switch (0|1)

**PC > Robot**

- `[G]`: reference angular speed of motor 0 (rad/s)
- `[H]`: reference angular speed of motor 1 (rad/s)
- `[I]`: reference angular speed of motor 2 (rad/s)
- `[J]`: reference angular speed of motor 3 (rad/s)
- `[K]`: PWM value of motors
  - `(value >> 24) & 0x03`: motor index (0..3)
  - `value & 0xFFFF`: PWM value (0..`kMotPWMmax`)
- `[L]`: solenoid (0|1)

## Usage

**Requirements**

- PlatformIO extension for VS Code

### Compilation

1. Clone the repository
   ```sh
   # Clone repository
   git clone git@github.com:5dpo/5dpo_ratf_firmware.git
   cd 5dpo_ratf_firmware

   # Open the folder as a project
   code .
   ```
2. Open `src/main.cpp`
3. Compile the project using the PlatformIO extension in VS Code
   (PlatformIO on left-side navigation bar > Project Tasks > Build)

### Run

1. Open `src/main.cpp`
2. Compile the project using the PlatformIO extension in VS Code
   (PlatformIO on left-side navigation bar > Project Tasks > Upload)

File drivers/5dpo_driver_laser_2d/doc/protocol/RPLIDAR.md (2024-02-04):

# RPLIDAR

Interface protocal applicable to RPLIDAR A and S series.

## Working States

- **Idle state:**
  - Default state (enter automatically after powering up / reset)
  - No output of ranging data
- **Request processing state:**
  - Enters state after receiving a request packet from host system
  - No scan operation and no ranging data
  - Only send out response data for request needing a response
- **Protection stop state:**
  - Device hardware error
  - Host system may query the laser's working status
  - No scan operations unless host system sends a reset request to reboot the
    lidar
- **Scanning state:**
  - Only when motor rotation speed is stable the RPLIDAR starts taking distance
    measurement and sending out the result data

### Scan mode and measurement frequency (>= FWv1.24)

| Scan Mode Name | Description | Max Sample Rate (sps) |
| :---: | :--- | :---: |
| Standard | Traditional mode | 16000 (S2) |
| Express | Traditional express mode |
| Boost | Performance priority mode (sample rate) |
| Sensitivity | Sensitivity priority mode (longer range, better sensitivity) |
| Stability | Stability priority mode (environment light elimination performance) |
| DenseBoost | Dense mode | 32000 (S2) |

## Packet Format

### Request packet

| Start Flag | Command | Payload Size | Payload Data | Checksum |
| :---: | :---: | :---: | :---: | :---: |
| 1B (0xA5) | 1B | 1B (optional) | 0-255B (optional) | 1B (optional) |

- **Start flag:** 0xA5
- **Command:** type of request
- **Payload size:** required if the current request carries extra payload data
- **Checksum:** after the payload data has been transmitted, compute checksum
  field from the previous sent data
  - `checksum = 0 (+) 0xA5 (+) CmdType (+) PayloadSize (+) Payload[0] (+) ... (+) Payload[n]`,
  where `(+)` represents OR-exclusive
- **Timing consideration:** all bytes within a request packet must be
  transmitted to RPLIDAR within 5 seconds

### Response packet

- If current request requires a response, always send a response descriptor
- Only send one descriptor packet during a request/response session

**Response descriptors**

| Start Flag (1) | Start Flag (2) | Data Response Length | Send Mode | Data Type |
| :---: | :---: | :---: | :---: | :---: |
| 1B (0xA5) | 1B (0x5A) | 30bits | 2bits | 1B |

- **Start flag:** 0xA5 + 0x5A to identify the start of a response descriptor
- **Data response length:** size of a **single** incoming data response packet
  in bytes
- **Send mode:** request/response mode of the current session
  - 0x0: single request - single response (only 1 data response packet)
  - 0x1: single request - multiple response (continuous data transmission)
  - 0x2 and 0x3: reserved for future use
- **Data type:** type of the incoming data
  - Possibility of choosing different data receiving and handling policy based
    on this field
  - Each type of response data has its own data format and packet length based
    on its type

## System Communication

### System command

| Request Name | Command | Payload | Response Mode | Description |
| :--- | :---: | :---: | :---: | :--- |
| Stop | 0x25 | N/A | No response | current state > idle |
| Reset | 0x40 | N/A | No response | reset / reboot RPLIDAR |
| Scan | 0x20 | N/A | Multiple response | enter scan state |
| Express scan | 0x82 | YES | Multiple response | enter scan state + highest speed |
| Force scan | 0x21 | N/A | Multiple response | enter scan state + no check rotation stability |
| Get info | 0x50 | N/A | Single response | send device info |
| Get health | 0x52 | N/A | Single response | send device health info |
| Get sample rate | 0x59 | N/A | Single response | send single sampling time |
| Get lidar conf | 0x84 | YES | Single response | get lidar configuration |

**Stop: 0xA5 + 0x25**

- Enter idle state
- Wait at least 1ms before sending another request

**Reset: 0xA5 + 0x40**

- Make RPLIDAR core to reset / reboot itself
- Useful whel RPLIDAR enters Protection Stop state
- After reset, return to idle state
- Wait at least 2ms before sending another request

**Scan: 0xA5 + 0x20**

- Lower sampling rate
  - **Note:** use Express scan for the best performance
- If already in scan state, stop current measurement and start new round of
  scanning
- Ignored when RPLIDAR in Protection Stop state

## Data Protocol

**Note:** RPLIDAR data communication adopts the little-endian mode and the
low-order mode in values with 2B.

### Scan command (0xA5 + 0x20)

**Response Descriptor**

| 0 | 1 | 2 | 3 | 4 | 5 | 6 |
| :---: | :---: | :---: | :---: | :---: | :---: | :---: |
| A5 | 5A | 05 | 00 | 00 | 40 | 81 |

- **Response mode:** 0x1 (single request - multiple response)
- **Data type:** 0x81

**Data Response Packet**

| 0 | 1 | 2 | 3 | 4 |
| :---: | :---: | :---: | :---: | :---: |
| QL | ANG | ANG | DIST | DIST |
| [Quality][~S][S] | [Angle LSB][C] | [Angle MSB] | [Dist LSB] | [Dist MSB] |

- Quality (6bits): quality of the current measurement sample related to the
  reflected laser pulse strength
- S: start flag bit of a new scan
  - QL[bit(0)] = 1: current and incomming packets belong to a new 360deg scan
  - Set to 1 for the first scan point of each scan frame
  - Inversed start flag bit may be used as a data check bit
- C: check bit
  - Constantly set to 1
  - May be used as a data check bit
- Angle: heading angle (deg) between 0deg and 360deg
  - Actual angle = angle / 64.0 deg
  - Clockwise (CW)
- Distance: measured object distance (mm)
  - Actual distance = distance / 4.0
  - Set to 0 when measurement invalid

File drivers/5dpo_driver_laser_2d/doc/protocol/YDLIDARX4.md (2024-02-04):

# YDLIDARX4

## Working Modes

- **Idle mode:**
  - Default mode
  - No output of ranging data
- **Scan mode:**
  - Continuous output of ranging data
- **Stop mode:**
  - Active when error occurs (when turning on the scanner, e.g., motor does not
    rotate, laser off, etc.)
  - Automatic turns off the output of ranging data
  - Feedbacks the error code

## System Communication

### Communication mechanism

1. **Device > X4:** System command
2. **X4:** Parsing command
3. **X4:** Switch mode
4. **X4 > Device:** Reply message
5. **Device:** Parsing command
6. **Device:** Retrieve data

### System command

| System Command | Description | Mode Switch | Response Mode |
| :---: | :--- | :---: | :---: |
| 0xA5 + 0x60 | Start scanning and export point cloud data | Scan | Continuous |
| 0xA5 + 0x65 | Stop and stop scanning | Stop | None |
| 0xA5 + 0x90 | Get device information | No | Single |
| 0xA5 + 0x91 | Get device health status | No | Single |
| 0xA5 + 0x80 | Soft restart | / | No response |

### Response messages

**Types of responses**

- No response
- Single response
- Continuous response

**Response message**

| Start Sign | Response Length | Response Mode | Type Code | Content |
| :---: | :---: | :---: | :---: | :---: |
| 16 bits | 30 bits | 2 bits | 8 bits | / |

| 0 | | 2 | | 4 | | 6 | 7 |
| :--- | :--- | :--- | :--- | :--- | :--- | :--- | :--- |
| LSB | MSB | LSB | MSB | LSB | [Mode] MSB | LSB | ... |

- **Start sign:** 0xA55A
- **Response length:** length infinite when answer mode is continuous
- **Response mode:** 2 bits
  - 0x0: single response
  - 0x1: continuous response
  - 0x2 and 0x3: undefined
- **Type code:** different system commands correspond to different types codes
- **Content:** data content (each system command has its own communication
  protocol)

## Data Protocol

**Note:** X4 data communication adopts the little-endian mode and the low-order
mode.

### Scan command (0xA5 + 0x60)

| 0 | | 2 | | 4 | | 6 | 7 |
| :--- | :--- | :--- | :--- | :--- | :--- | :--- | :--- |
| A5 | 5A | 05 | 00 | 00 | [Mode] 40 | 81 | ... |

- **Length:** ignore!
- **Response mode:** 0x1 continuous (= high part of the 6th bit)
- **Type code:** 0x81

**Content (variable)**

| 0 | | 2 | | 4 | | 6 | | 8 | | 10 | | 12 | | .. | .. |
| :--- | :--- | :--- | :--- | :--- | :--- | :--- | :--- | :--- | :--- | :--- | :--- | :--- | :--- | :--- | :--- |
| PH | | CT | LSN | FSA | | LSA | | CS | | S1 | | S2 | | .. | .. |
| LSB | MSB | LSB | MSB | LSB | MSB | LSB | MSB | LSB | MSB | LSB | MSB | LSB | MSB | .. | .. |

| Content | Name | Description |
| :---: | :---: | :--- |
| PH(2B) | Package header | Fixed at 0x55AA (low in front, high in back) |
| CT(1B) | Package type | CT[bit(0)] = 1 start of a round of data; CT[bit(0)] = 0 indicates the point cloud data package. CT[bit(7:1)] are reserved bits |
| LSN(1B) | Sample quantity | Number of sampling points in current package. Only one initial point in the zero package (value = 1). |
| FSA(2B) | Start angle | Angle of the first sample point. |
| LSA(2B) | End angle | Angle of the last sample point. |
| CS(2B) | Check code | 2B exclusive OR to check the current data package. |
| Si(2B) | Sample data | Distance data of the sampling point. |

- Start bit & scan frequency analysis
  - CT[bit(0)] = 0: point cloud package
  - CT[bit(0)] = 1: start package
    - LSN = 1 (#Si = 1)
    - CT[bit(7:1)]: scan frequency information
      - F = CT[bit(7:1)]/10
- Distance analysis:
  - Di = Si / 4
- Angle analysis:
  - Data structure:
    - LSB: [Ang_q2[6:0] | C], where C is fixed at 1 (check bit)
    - MSB: [Ang_q2[14:7]]
  - 1st level: obtain initial value of the angle
    - Angle FSA = (FSA >> 1) / 64
    - Angle LSA = (LSA >> 1) / 64
    - Angle i = diff(Angle) / (LSN - 1) * (i - 1) + Angle FSA, i = 2, 3, ...,
      LSN - 1
      - diff(Angle) is clockwise angle difference from the starting angle
        (uncorrected value) to the ending angle (uncorrected value)
      - LSN is the number of package samples in the current frame
  - 2nd level: correct initial value of the angle
    - Angle i = Angle i + AngCorrect i
    - AngCorrect i:
      - (Distance i == 0) AngCorrect i = 0
      - (ELSE) AngCorrect i = tand^(-1) (21.8 * (155.3 - Distance i) /
        (155.3 * Distance i))
- Check code parsing:
  - CS = XOR 1..end (Ci)
    1. PH(2B)
    2. FSA(2B)
    3. S1(2B)
    4. ...
    5. [ CT(2B) | LSN(2B) ]
    6. LSA(2B)

### Device information (0xA5 + 0x90)

| 0 | | 2 | | 4 | | 6 | 7 |
| :--- | :--- | :--- | :--- | :--- | :--- | :--- | :--- |
| A5 | 5A | 14 | 00 | 00 | [Mode] 00 | 04 | ... |

- **Length:** 0x00000014
- **Response mode:** 0x0 single
- **Type code:** 0x04

**Content (20B)**

| 0 | 1 | 2 | 3 | 4 | 5 | .. | 19 |
| :--- | :--- | :--- | :--- | :--- | :--- | :--- | :--- |
| Model | FW version | FW version | HW version | Serial number | Serial number |  .. | Serial number |

- **Model number (1B):** YLIDAR X4 = 0x06
- **Firmware version (2B):**
  - LSB: major version number
  - MSB: minor version number
- **Hardware version (1B)**
- **Serial number (16B):** the only factory serial number

### Health status (0xA5 + 0x91)

| 0 | | 2 | | 4 | | 6 | 7 |
| :--- | :--- | :--- | :--- | :--- | :--- | :--- | :--- |
| A5 | 5A | 03 | 00 | 00 | [Mode] 00 | 06 | ... |

- **Length:** 0x00000003
- **Response mode:** 0x0 single
- **Type code:** 0x06

**Content (3B)**

| 0 | 1 | 2 |
| :--- | :--- | :--- |
| Status | Error code | Error code |

- **Status code (1B):**
  - 0x0: runs normally
  - 0x1: warning
  - 0x2: incorrect behavior
- **Error code (2B):**
  - 0x00: runs wo/ any error
  - Specific error code

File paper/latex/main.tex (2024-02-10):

\documentclass[conference]{IEEEtran}
\IEEEoverridecommandlockouts

%%%%%%%%%%%%%%%%%%%%%%%%%
%%%% LATEX PACKAGES %%%%%
%%%%%%%%%%%%%%%%%%%%%%%%%

\usepackage{amsmath,amssymb,amsfonts}
\usepackage{algorithmic}
\usepackage{graphicx}
\usepackage[font=small]{caption}
\usepackage[font=footnotesize]{subcaption}
\usepackage{textcomp}
\usepackage{xcolor}
\usepackage{hyperref}
\usepackage{svg}
\usepackage{enumitem}
\usepackage[backend=biber,
            %style=apa,
            %style=numeric,
            style=numeric-comp,
            bibstyle=numeric,
            %citestyle=authoryear-comp,
            citestyle=numeric-comp,
            %sorting=nyt,
            sorting=none,
            maxnames=8,
            minnames=3
            %maxcitenames=2,
            %mincitenames=1
            ]{biblatex}

\usepackage{easyReview} % use to help review the paper (https://ctan.org/pkg/easyreview)

%%%%%%%%%%%%%%%%%%%%%%%%%%%%
%%%%% USER DEFINITIONS %%%%%
%%%%%%%%%%%%%%%%%%%%%%%%%%%%

\addbibresource{references.bib}

\def\BibTeX{{\rm B\kern-.05em{\sc i\kern-.025em b}\kern-.08em
    T\kern-.1667em\lower.7ex\hbox{E}\kern-.125emX}}

\newcommand{\orcid}[1]{\href{https://orcid.org/#1}{}}

\newcommand{\etal}{\textit{et.~al.}}

\begin{document}

%%%%%%%%%%%%%%%%%
%%%%% TITLE %%%%%
%%%%%%%%%%%%%%%%%

\title{System Framework for the\\Robot@Factory 4.0 Competition\\
\thanks{This work is financed by National Funds through the Portuguese funding agency, FCT -- Fundação para a Ciência e a Tecnologia, within project LA/P/0063/2020
(DOI: \href{https://doi.org/10.54499/LA/P/0063/2020}{10.54499/LA/P/0063/2020}).}}

%%%%%%%%%%%%%%%%%%%%%%%%%%%%%%%%%%%%%%%%%%%%%%
%%%%% AUTHORS + AFFILIATIONS INFORMATION %%%%%
%%%%%%%%%%%%%%%%%%%%%%%%%%%%%%%%%%%%%%%%%%%%%%

\author{%
\IEEEauthorblockN{%
Ricardo B. Sousa\IEEEauthorrefmark{1}\IEEEauthorrefmark{2}~\orcid{0000-0003-4537-5095},
Cl\'{a}udia D. Rocha\IEEEauthorrefmark{2}\IEEEauthorrefmark{3}~\orcid{0000-0001-7254-0346},
Jo\~{a}o G. Martins\IEEEauthorrefmark{1}\IEEEauthorrefmark{2}~\orcid{0000-0002-6567-4802},
Jo\~{a}o Pedro Costa\IEEEauthorrefmark{1},\\
Jo\~{a}o Tom\'{a}s Padr\~{a}o\IEEEauthorrefmark{1},
Jos\'{e} Maria Sarmento\IEEEauthorrefmark{2}\IEEEauthorrefmark{3}~\orcid{0000-0002-4332-9645},
Jos\'{e} Pedro Carvalho\IEEEauthorrefmark{1}\IEEEauthorrefmark{4}~\orcid{0009-0008-3416-5694},
Maria S. Lopes\IEEEauthorrefmark{1}\IEEEauthorrefmark{2}~\orcid{0009-0001-7216-2469},\\
Paulo G. Costa\IEEEauthorrefmark{1}\IEEEauthorrefmark{2}~\orcid{0000-0002-4846-271X},
Ant\'{o}nio Paulo Moreira\IEEEauthorrefmark{1}\IEEEauthorrefmark{2}~\orcid{0000-0001-8573-3147}}
%
\IEEEauthorblockA{%
\IEEEauthorrefmark{1}Faculty of Engineering, University of Porto (FEUP), 4200-465 Porto, Portugal\\
Email: \texttt{up\{\href{mailto:up201503004@edu.fe.up.pt}{201503004},%
\href{mailto:up201806222@edu.fe.up.pt}{201806222},%
\href{mailto:up201806431@edu.fe.up.pt}{201806431},%
\href{mailto:up202108766@edu.fe.up.pt}{202108766},%
\href{mailto:up201806775@edu.fe.up.pt}{201806775}\}@edu.fe.up.pt}\\
\texttt{\{\href{mailto:jpcarvalho@fe.up.pt}{jpcarvalho},%
\href{mailto:paco@fe.up.pt}{paco},%
\href{mailto:amoreira@fe.up.pt}{amoreira}\}@fe.up.pt}%
}
\IEEEauthorblockA{%
\IEEEauthorrefmark{2}CRIIS -- Centre for Robotics in Industry and Intelligent Systems\\
INESC TEC -- Institute for Systems and Computer Engineering, Technology and Science, 4200-465 Porto, Portugal\\
Email: \texttt{\{\href{mailto:claudia.d.rocha@inesctec.pt}{claudia.d.rocha},%
\href{mailto:jose.m.sarmento@inesctec.pt}{jose.m.sarmento}\}@inesctec.pt}%
}
\IEEEauthorblockA{%
\IEEEauthorrefmark{3}School of Science and Technology\\
University of Tr\'{a}s-os-Montes and Alto Douro (UTAD), 5000-801 Vila Real, Portugal%
}
\IEEEauthorblockA{%
\IEEEauthorrefmark{4}C2SR -- Cyber-Physical Control Systems and Robotics\\
SYSTEC -- Research Center for Systems and Technologies, 4200-465 Porto, Portugal%
}
}

\maketitle

%%%%%%%%%%%%%%%%%%%%%%%%%%%%%%%
%%%%% ABSTRACT + KEYWORDS %%%%%
%%%%%%%%%%%%%%%%%%%%%%%%%%%%%%%

\begin{abstract}
Robotic competitions stand as platforms to propel the forefront of robotics research while nurturing STEM education, serving as hubs of both applied research and scientific innovation.
In Portugal, the Portuguese Robotics Open~(FNR) is a national event with several robotic competitions, including the Robot@Factory~4.0 competition.
This competition presents an example of deploying autonomous robots on a factory shop floor.
Although the literature has works proposing system frameworks for the original version of the Robot@Factory competition, none of them proposes a system framework for the Robot@Factory~4.0 version that presents the hardware, firmware, and software to complete the competition and achieve autonomous navigation.
So, this paper proposes a complete system framework for the Robot@Factory~4.0 competition that is modular and open-access, enabling future participants to use and improve it in future editions.
This work is the culmination of all the knowledge acquired by winning two editions of the competition.
\end{abstract}

\begin{IEEEkeywords}
autonomous mobile robots, robot competitions, robot at factory 4.0
\end{IEEEkeywords}

%%%%%%%%%%%%%%%%%%%%%%%%%%%%
%%%%% DOCUMENTION BODY %%%%%
%%%%%%%%%%%%%%%%%%%%%%%%%%%%

\section{Introduction}\label{sec:intro}

Since 1997, the RoboCup\footnote{\label{note:robocup}\url{https://www.robocup.org/}} federation has organised international robot soccer competitions, including Small and Middle Size League (SSL and MSL, respectively) robots and humanoids, and more recently, competitions focused on service (RoboCup@Home) and industrial (RoboCup@Work) autonomous robots.
Another example is the Formula Student\footnote{\url{https://www.imeche.org/events/formula-student}} competition, which has been held in Europe since 1999. This event includes several categories (combustion, electric, hybrid, and driverless autonomous systems) while being an educational engineering platform in several fields, such as robotics, computer science, mechanical, and electrical and computer engineering.
More recently, the F1TENTH~\cite{literature:competitions:f1tenth} and the Indy Autonomous Challenge~(IAC)~\cite{literature:competitions:indy} were created to push further the research on autonomous systems and also serve as STEM education platforms for students.

In Portugal, the Portuguese Robotics Open~(FNR)\footnote{\label{note:fnr}\url{https://www.festivalnacionalrobotica.pt/}} is an event hosting several competitions divided into major and junior categories.
These competitions include qualification events to decide the Portuguese teams participating in the RoboCup, international championships, autonomous driving, dragster, and the Robot@Factory Lite and Robot@Factory~4.0 competitions, which are more oriented to industrial cases.
In particular, the Robot@Factory~4.0 competition aims to represent the deployment of autonomous mobile robots on a factory shop floor. The robots should be able to transport materials between warehouses or machines that process those materials, considering the robots' ability to self-localise and navigate in order to avoid collisions with the walls.

The current literature has works oriented toward the original and present versions of the Robot@Factory competition hosted at FNR (Robot@Factory and Robot@Factory~4.0, respectively).
Ribeiro~\etal~\cite{literature:ratf:ribeiro-2017} presented their design and development path towards the robot used to participate in the original version of the competition.
The robot was a three-wheeled omnidirectional robot with five processing units (including a Raspberry Pi 2 Model B and two Arduino Mini), a 2D laser scanner, and an Inertial Measurement Unit (IMU) used to obtain a pose estimation.
Similarly, Pinto~\etal~\cite{literature:ratf:pinto-2023} also proposed a three-wheeled omnidirectional robot to participate in the original competition.
The proposed framework used wheeled odometry and 2D laser data to estimate the robot pose with the PerfectMatch~\cite{literature:ratf:pinto-2023:perfect-match} algorithm, while only using a single processing unit, namely, a Raspberry Pi 3.
Finally, Braun~\etal~\cite{literature:ratf:braun-2024} presented the development of a four-wheeled mecanum platform specifically designed for the Robot@Factory~4.0 competition, with a Raspberry Pi 4 and an Arduino Mega 2560 as processing units. 
This work focused on the mechanical design and electronics of the robot, including the description of the sensory perception system composed by a camera and a 2D laser scanner.
In conclusion, the works of Ribeiro~\etal~\cite{literature:ratf:ribeiro-2017} and Pinto~\etal~\cite{literature:ratf:pinto-2023} are not intended for the present version of the Robot@Factory competition, while the work of Braun~\etal~\cite{literature:ratf:braun-2024} does not cover the software architecture and implementation part of the robot.

Thus, this paper proposes a modular and open-access system framework for an autonomous robot to be able to participate in future editions of the Robot@Factory~4.0 competition.
The description of the proposed framework includes the hardware, firmware, and software implemented by the 5dpo Robotics Team\footnote{\url{https://5dpo.github.io/}} that led the team to win two consecutive editions of the competition.
All the code relative to firmware and software developed within the context of the competition, 3D models of the robot parts, and additional documentation are available in a public GitHub repository\footnote{\label{note:repo}\url{https://github.com/5dpo/5dpo_ratf_2023}}.
Indeed, this repository containing the implementation of the proposed framework may be used by future participants in the competition to have an initial start on their development and push it even further to foster their STEM education knowledge.
To the best of the authors' knowledge, and according to the related works information found in the literature, no framework encompasses hardware, software, and system integration to allow building an entire robot system for the Robot@Factory~4.0 competition.

The remaining of this paper is organised as follows.
Section~\ref{sec:ratf} presents a brief summary of the current version of the Robot@Factory 4.0 competition.
Section~\ref{sec:system} describes the architecture of the proposed system framework.
Then, Sections~\ref{sec:hw}, \ref{sec:fw}, and \ref{sec:sw} characterise the hardware, firmware, and software implemented and used in the competition, respectively.
Section~\ref{sec:tests} presents the results originated from the participation in two editions of Robot@Factory~4.0.
Lastly, Section~\ref{sec:conclusions} formulates the final conclusions and future work.

\section{Robot@Factory 4.0 Competition}\label{sec:ratf}

The competition presents the problem of deploying autonomous mobile robots on a factory shop floor (illustrated in Figure~\ref{fig:ratf:track-2023}).
One or more robots should transport materials between warehouses or machines, depending on the type of materials received in the input warehouse.
The robots will transport three different parts from the incoming warehouse: blue, green, and red boxes.
The first is considered a final part; thus, it is sent directly to the output warehouse.
The second one is an intermediate part that must receive a transformation to a blue box at either machines A or B.
Lastly, the red box must suffer two transformations, first on machine A to a green part, and then on B to a blue box.
Furthermore, the competition is divided into three rounds. The rounds are distinguished by the type of parts received in the incoming warehouse: only blue parts are considered in the first round, in the second one may exist some green parts (usually, two boxes), and in the third round may have both green and red parts (usually, two and one boxes, respectively).
The robot must communicate with a Wi-Fi server to get which part types are available for each slot in the incoming warehouse at the start of each run.

\begin{figure}[!t]
\centering
\centerline{\includesvg[height=0.7\columnwidth]{figures/ratf-track_2023.svg}}
\caption[Shop floor of the Robot@Factory 4.0 2023 edition composed by warehouses (input on the top-left and output on the bottom-right of the floor), machines (middle wall markings, where the machines A are on the left and B on the right side), and ArUco markers.]{Shop floor of the Robot@Factory 4.0 2023 edition composed by warehouses (input on the top-left and output on the bottom-right of the floor), machines (middle wall markings, where the machines A are on the left and B on the right side), and ArUco markers~\cite{ratf:github-repo}.}
\label{fig:ratf:track-2023}
\end{figure}

As for the robot design, each robot must fit into a $30\times30$~cm rectangle with a maximum height of 30~cm.
The robot must be completely autonomous and cannot communication with any type of external systems that are not provided by the organisation.
Unlike the original version of the Robot@Factory competition, the shop floor has no guiding lines nor outer walls delimiting the shop floor area.
The teams can use the ArUco markers on the floor for localisation (the guidelines of the competition available in \cite{ratf:github-repo} present the ground-truth position of those).
Additionally, the teams can place their own markers (e.g., reflectors or poles) near the corners of the factory, providing that these do not exceed an occupied area of $10\times 10$~cm and a maximum height of 50~cm.

In terms of the final classification, the team with the highest total number of parts correctly transported to the outgoing warehouse or to a machine is the winner.
In case of teams with the same total number of points, the first criteria is the number of correctly places parts in the outgoing warehouse, and the second criteria is the shortest time to finish the round.

\section{System Architecture}\label{sec:system}

The system framework proposed in this paper and illustrated in Figure~\ref{fig:system-architecture} is composed of three elements: all the components and mechanics related to the robot (motors, sensors, actuators), the firmware layer to interact with low-level devices (including motors speed reading and control) running in an Arduino~Mega~2560, and the software executing in a Raspberry~Pi~4B~4G (drivers to interact with the firmware and other devices, localisation and navigation modules).
First, the robot is a four-wheeled omnidirectional platform designed in the scope of the Robot@Factory~4.0 competition, using a 3D printer to make the parts of the platform. The robot includes a switch and a solenoid to sense and transport the boxes.
Next, the firmware layer controls the motors' angular speed, counts the encoder quadrature pulses, reads the switch state, and actuates the solenoid according to the software.
Then, the software executes Robot Operating System~(ROS) nodes implemented in C++ to interact with the firmware and other devices (including the 2D laser scanner), estimate the robot pose, provide a Human-Machine Interface~(HMI) interface based on \texttt{rviz}, and enable the autonomous navigation of the robot to execute the desired tasks.
The following sections explain each element of the system framework in depth.

\begin{figure}[!t]
\centering
\centerline{}
\caption{System architecture proposed in this paper for the Robot@Factory~4.0 competition.}
\label{fig:system-architecture}
\end{figure}

\section{Hardware}\label{sec:hw}

\subsection{Robot motion}

In terms of the robot motion, the four-wheeled omnidirectional platform designed in the scope of the competition is illustrated in Figure~\ref{fig:robot}.
This platform uses 60~mm aluminium mecanum wheels, where the distance between the front-back and left-right wheels is 0.152~m and 0.193~m, respectively.
As a consequence of using four mecanum wheels, the robot has holonomic kinematics, originating that the robot's linear and angular velocities are decoupled from each other (e.g., the robot can manoeuvre around obstacles without affecting the orientation)~\cite{book:intro-robotics}.
Indeed, this design choice results in an increased flexibility in terms of path planning and trajectory control, where the robot may rotate along the trajectory without requiring to do on-the-spot rotations.

\begin{figure}[!t]
\centering
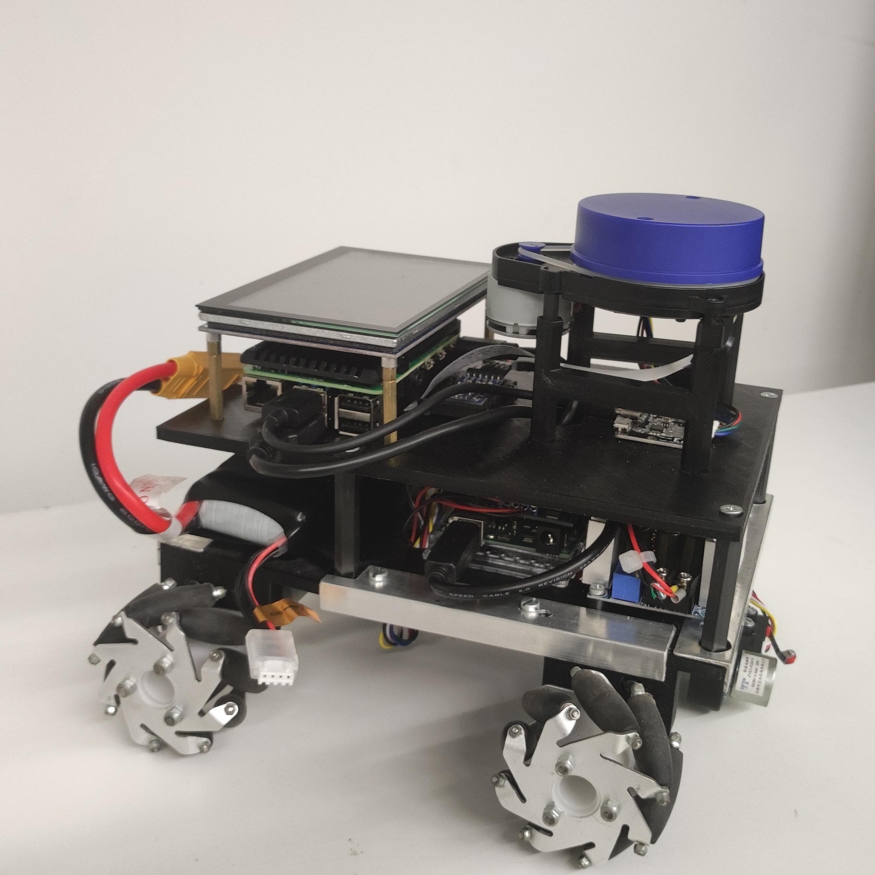
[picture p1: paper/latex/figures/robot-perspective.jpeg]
\subfloat[][]{%
\label{fig:robot:cool-pic}}
\linebreak
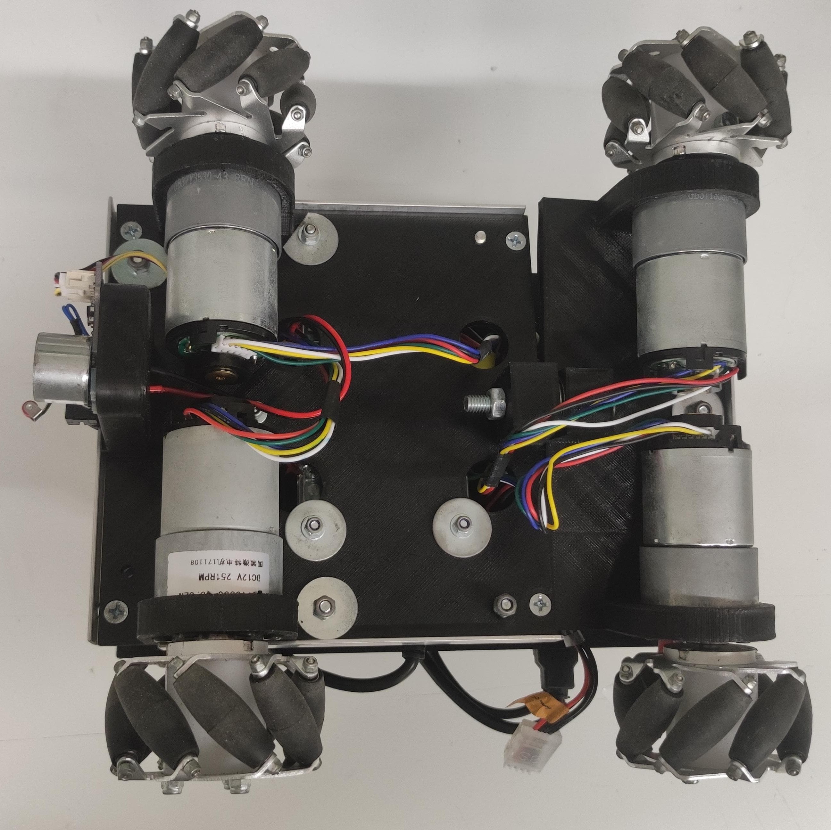
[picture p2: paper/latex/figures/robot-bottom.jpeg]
\subfloat[][]{%
\label{fig:robot:suspension}}
\caption{Four-wheeled omnidirectional platform designed in the scope of the competition:
(a) the robot;
(b) the bottom with the suspension.}
\label{fig:robot}
\end{figure}

Furthermore, the motors chosen are 12V~DC motors with 251~rpm at no load from DFRobot.
The motors include a 43.7:1 metal gearbox and integrated quadrature encoders based on the Hall effect.
These encoders have a resolution of 16 counts per revolution of the motor shaft, resulting in approximately 700~counts of the gearbox's output shaft.
If the firmware can process the pulses, this setup results in a resolution of 2800~pulses per revolution on the robot's wheels.

An additional design constraint must be accounted for because the robot has four wheels.
Conventionally, the static stability of a robot requires a minimum of three wheels, where the triangle formed by the ground contact points must contain the centre of gravity. The latter is ensured in the proposed platform by most of the components being in the volume between the front and back wheels.
However, once the number of contact points exceeds three, the geometry requires some form of flexible suspension on uneven terrain~\cite{book:intro-robotics}.
Even though the floor of the competition should be flat and even, Figure~\ref{fig:robot:suspension} shows the suspension put in the robot to be compatible with terrain with minor imperfections in terms of its flatness.

\subsection{Processing unit}

Next, an Arduino Mega 2560 executes the firmware described in this paper. This microcontroller board is compatible with several open-source libraries, including the SPI\footnote{\href{https://www.arduino.cc/reference/en/language/functions/communication/spi/}{https://www.arduino.cc/reference/en/language/functions/communication/\\spi/}} (communication with SPI devices) and TimerOne~\&~TimerThree\footnote{\label{note:timers-lib}\url{https://www.pjrc.com/teensy/td_libs_TimerOne.html}} (implementation of timers with PWM pins) libraries used in this work.
Moreover, the 5V operating voltage of the Arduino~Mega is directly compatible with the voltage of the encoders of the motors and the electromagnet actuation.

As for the software, the Raspberry~Pi~4B~4GB executes all the ROS nodes implemented in C++.
Given that this paper uses ROS 1 Noetic, the Operating System~(OS) running in the Raspberry Pi was the Raspberry OS (Legacy) based on Debian Buster.
However, the OS Ubuntu~20.04 may also be used instead of Raspbian, in case there is no need for graphical output.
Also, the advantages of using Raspberry~Pi are its compatibility with the Raspberry~Pi Camera module (e.g., for ArUco markers detection) and its 40 General-Purpose Input/Output~(GPIO) pins compatible with SPI and I2C devices.

\subsection{Sensors}

In terms of the sensory system on the robot, in addition to the wheel odometry data obtained from the encoders, the robot is equipped with a 2D laser scanner and an IMU.
The first is a YDLIDAR~X4 based on the principle of triangulation.
This laser has a 360º Field-of-View~(FoV), a range between 0.12~m and 10~m, and a typical scanning frequency and angle resolution of 7~Hz (using the device interface to connect and power up the laser through a USB connection) and 0.5º, respectively.
Considering the maximum area of $1.7\times1.2$~m for the shop floor defined in the competition rules, the sensor is considerably suitable for this application.
However, other alternatives based on Time-of-Flight~(ToF) technologies, such as the DTOF~LD19 and RPLIDAR~S2 lasers, may provide more precise distance data.
As for the IMU, the sensor employed on the robot is the Waveshare 10 Degrees-of-Freedom~(DoF).
This IMU is a low-cost sensor with an accelerometer, magnetometer, gyroscope, and temperature sensor.
However, only the accelerometer and gyroscope data are used in the scope of this paper. The data communication between IMU and Raspberry~Pi is through an I2C bus.

Even though camera data is not used in this paper, the four-wheeled omnidirectional platform illustrated in Figure~\ref{fig:robot} is also equipped with an RGB Raspberry Pi Camera Board v2.
This camera has a sensor with 8MP and a resolution of up to 1080p.
The main advantages of using this camera are its ribbon cable compatibility with the CSI port on the Raspberry Pi, native drivers for the camera in the Raspberry Pi, and compatibility with the OpenCV computer vision library.

\subsection{Electronics}

As for powering up the robot, the platform has a Gens Ace 5000mAh battery with a 3S cell configuration and an 11.1V nominal voltage.
The battery directly powers the wheels' motors and the Arduino~Mega.
Although 
Furthermore, a 300W DC/DC buck converter compatible with the conversion from 6--40V in the input to 1.2--36V in the output (maximum of 20A) creates a second voltage rail of 5V.
This rail powers up the Raspberry~Pi~4B and the electromagnet.
Although it would be advisable to have a voltage regulator between the battery and the other components, the approach taken in the platform simplifies as much as possible the electronics of the system.

Moreover, the Raspberry Pi powers up the 2D laser scanner and the IMU through the USB connection and the GPIO interface, respectively.
In order to control the motors' angular speed, the system must have an electronic board able to generate PWM signals for the motors.
Thus, the Arduino~Mega used in the platform also has the Adafruit Motor Shield.
This shield allows to drive up to four DC motors, communicating with the microcontroller over I2C.

\subsection{3D modelling}

Lastly, all the parts composing the structure of the omnidirectional platform are 3D printed in PLA.
These parts are available in STEP files in the public repository\footref{note:repo}.
The leading software used to design the parts was originally the OpenSCAD open-source modeller, and then, the team transitioned to AutoDesk~Fusion~360.
The latter has both free personal and academic licenses available for use.
Even so, STEP files are compatible with other 3D modelling software such as FreeCAD and SolidWorks, allowing to use other programs to perform modifications in the original parts.

\section{Firmware}\label{sec:fw}

The robot's firmware is implemented in the Arduino Mega 2560 as a PlatformIO project (the latter has extensions for both CLion and Visual Studio Code).
This firmware includes counting the encoders' pulses, angular speed control of the motors, the serial communication with the Raspberry~Pi through a UART/USB connection, and the simple logic associated with reading the switch state and actuating the solenoid.

\subsection{Wheel encoders}

First, relative to counting the encoders' pulses, Figure~\ref{fig:fw:encoders} illustrates the quadrature inherently related to a two-channel (A and B) encoder.
Considering that the logical values of the two channels are known for the current time instant $k$ and the previous instant $k-1$,  there are 16 possible possibilities for all possible logic values of the last and current states of the two channels (presented in Table~\ref{tab:fw:encoders}).
Thus, the firmware developed for the framework proposed in this paper employs a lookup table to speed up the encoders' reading, being to attach an interruption to read the channels' logic values at 50~kHz.
This periodic interruption is implemented using the TimerOne library\footref{note:timers-lib}.
Even though other boards, such as the Raspberry Pi Pico and the Teensy ones, have programmable input/output machines that may improve even further the frequency of checking the channels and counting the pulses (avoiding skipping pulses due to higher angular speeds of the motors), the Arduino Mega does not offer that possibility.

\begin{figure}[!t]
\centering
\centerline{}
\caption{Encoders signals example.}
\label{fig:fw:encoders}
\end{figure}

\input{tables/encoders}

Furthermore, there are two occasions in Table~\ref{tab:fw:encoders} where the delta of the pulse counters is~0.
One of them is when the previous state is maintained in the current instant, meaning that the wheel did not move.
The other situation is when a transition in the quadrature of the encoders is skipped, e.g., having the previous state $\{A,B\}_{k-1}={0,0}$ and the current one $\{A,B\}_{k}={1,1}$.
This situation does not reveal the wheel's direction, thus setting the delta to 0 to avoid counting erroneous pulses.

Regarding the resolution of counting the encoders' pulses, as stated in Section~\ref{sec:hw}, the encoders in the omnidirectional platform have a resolution of 16~counts per revolution on the motors' shaft.
The approach implemented in this paper can process the quadrature of the encoders, quadrupling the resolution.
Consequently, the final resolution obtained in the firmware is~64 and 2796.8~pulses per revolution on the motors' shaft and at the wheels, respectively (the latter considering the 43.7 reduction ratio in the motors' gears). This final resolution corresponds to 0.128º/pulse at the wheel.

\subsection{Wheel angular speed control}

The control of the motors' angular speed is similar to the methodology presented in Sousa~\etal~\cite{5dpo:sousa-2021}.
Proportional-Integrative~(PI) controllers set the motors' input voltage. Considering that the motors have a dead zone, a Hammerstein nonlinear block is used to compensate for the existence of that zone.
Then, the windup effect is compensated by limiting the voltage computed from the PI controllers and the Hammerstein block to the maximum value supported by the motors.
When the voltage exceeds these limits, the integration part of the PI controller remains unchanged.
Given that PWM signals can be used to control the DC motors, these signals are directly handled by the Adafruit Motor Shield with a frequency of 1.6~KHz (the maximum value allowed by the shield).
The communication between the shield and the Arduino Mega is through an SPI connection.

\subsection{Serial communication}

As for exchanging data between the firmware and the software modules, this data transmission is handled over a serial communication between the Raspberry~Pi and the Arduino~Mega.
The serial port's baud rate is 115200~bps, which is considered a safe setup in terms of timing errors.

The channels library\footnote{\url{https://github.com/P33a/MeArmControlVarSpeed}} manages the data protocol for the communication.
This paper employs the version that puts the hexadecimal representation of the data as ASCII characters in the communication stream.
Indeed, the data frame of this version is as follows: the first byte is a plain letter in ASCII format representing a channel, and the following 8 bytes are the hexadecimal representation of 4-byte data packets as ASCII characters (0--9, A--F).
The channel's letter can be any letter between a--z and G--Z.
Even though the channel's library has a binary form to compact the data part of the frame from 8 to 4~bytes, being more efficient, plain ASCII greatly facilitates the debugging of the firmware data streams by using a simple serial monitor.
Thus, the channels configuration used in the firmware is the following one:
\begin{itemize}[nosep]
\item Arduino Mega $\rightarrow$ Raspberry Pi:
  \begin{itemize}[nosep]
  \item \texttt{g}: pulse count of the back-right wheel (ticks)
  \item \texttt{h}: pulse count of the back-left wheel (ticks)
  \item \texttt{i}: pulse count of the front-right wheel (ticks)
  \item \texttt{j}: pulse count of the front-left wheel (ticks)
  \item \texttt{k}: interval time between control cycles (us)
  \item \texttt{r}: reset signal
  \item \texttt{s}: switch signal
  \end{itemize}
\item Raspberry Pi $\rightarrow$ Arduino Mega:
  \begin{itemize}[nosep]
  \item \texttt{G}: reference speed of the back-right wheel (rad/s)
  \item \texttt{H}: reference speed of the back-left wheel (rad/s)
  \item \texttt{I}: reference speed of the front-right wheel (rad/s)
  \item \texttt{J}: reference speed of the front-left wheel (rad/s)
  \item \texttt{K}: PWM value of the motors:
    \begin{itemize}[nosep]
    \item (value $>>$ 24) \& 0x03: motor index (0..3)
    \item (value) \& 0xFFFF: PWM value (0..max)
    \end{itemize}
  \item \texttt{L}: solenoid actuation
  \end{itemize}
\end{itemize}

This configuration allows the communication of the encoders' pulse counters, the desired angular speed for the motors, and the switch and solenoid signals required to interact and transport the boxes between locations between the two processing units in the omnidirectional platform.
The interval time is to monitor the control of the angular speed control and the reset signal to reinitialise the firmware driver in the software.
Additionally, channel \texttt{K} is to actuate the PWM directly (and so, being able to set the voltage of the motors), allowing a possible automatic calibration of the PI parameters using the software to set the voltage of the motors and logging the angular speed after processing the rate of pulses per second read from the encoders.

\section{Software}\label{sec:sw}

In terms of the software components of the system framework, all the software is developed in C++ and ROS~1~Noetic and is executed in the Raspberry Pi 4B 4GB.
The software includes the drivers developed in the scope of the competition, the robot localisation estimation and its integration with the laser scanner, wheeled and inertial odometry, autonomous navigation through the shop floor, and the HMI interface.

\subsection{Drivers}

As previously mentioned in Section~\ref{sec:fw}, the communication between the firmware and software is made through a serial port~(USB/UART) using the channels protocol.
Consequently, from the software side, a driver was specifically developed to handle the serial communication with the microcontroller and make the bridge between ROS messages and data processed by the firmware.
Similarly, the communication between the 2D laser scanner and the Raspberry Pi is also through a serial connection with a USB cable.
In this case, another driver was developed to interpret the data received from the YDLIDAR X4 and build a point cloud ROS message after a full 360º scan is processed by the driver.
These two drivers are based on an open-source asynchronous implementation over Boost.Asio\footnote{\url{https://github.com/fedetft/serial-port/tree/master/4_callback}}.
This implementation had to be modified to be compatible with the laser baud rate (128000~bps). The latter is incompatible with the original Boost.Asio implementation of serial port communication, requiring interaction with the OS termios interface to set the custom baud rate.

\subsection{Robot localisation}

The system framework proposed in this paper considers three sensor sources to estimate the robot pose: wheel encoders, IMU, and the 2D laser scanner.
First, wheeled odometry uses the encoders' data to estimate the robot's pose relative to a previous instant.
This estimation follows the same equations presented in Sousa~\etal~\cite{5dpo:sousa-2022} for the four-wheeled omnidirectional steering geometry to estimate the linear and angular displacements of the robot.
In the case of the IMU, this sensor was added later in the preparation phase for the 2023 edition to improve the odometry estimation of the robot pose, especially in linear and angular velocities higher than 0.5~m/s and 2~rad/s, respectively (even when scaling the velocities when one of the motors are saturated).
The robot\_pose\_ekf ROS node\footnote{\url{https://wiki.ros.org/robot_pose_ekf}} is responsible to fuse the wheeled odometry and IMU data estimations, where the 3D orientation data from the IMU improve the 2D pose of wheeled odometry.
Then, the laser data is used to detect beacons in the form of cylindrical poles with a 9~cm diameter to update the robot pose with an Extended Kalman Filter~(EKF)~\cite{book:intro-robotics}.
The methodology to extract the centre of the perceived poles is to use the current pose of the robot and cluster the laser points near the points expected to have poles.
The centroid of each cluster is assumed as the position of the pole perceived at each instant.

As for the EKF framework, the prediction step follows the kinematic equations in~\cite{5dpo:sousa-2022}. These equations update the current robot pose given the linear and angular displacements between two consecutive instants. So, the prediction step becomes independent of the odometry source used for the filter (wheeled-odometry only or fusing with IMU data).
In terms of the update step, Figure~\ref{fig:localisation} illustrates the robot when observing a beacon $B_i$.
The state of the filter ($X$) is the transformation of the robot ($\{X^R,Y^R\}$) w.r.t. the world ($\{X^W,Y^W\}$) coordinate frame, where $X=\left[R|t\right]\in SE(2)$. The Euclidean representation of this state is $X=\left(x,y,\theta\right)^T$, where $x$ and $y$ are the 2D translation and $\theta$ is the heading of the robot.
Furthermore, the ground-truth position of the beacon $B_i$ w.r.t. the world ($p_{b,i}$) is known, considering the centre of the coordinate frame being centred in the shop floor and that the position of the beacons could be measured with a metric tape.
Consequently, Equation~\ref{eq:ekf:h} represents the predicted beacon position w.r.t. the robot frame ($\tilde{p}_{b,i}$).
Considering the measurement $z$ being the distance ($d_{b,i}$) and heading ($\theta_{b,i}$) of the beacon w.r.t. the robot (illustrated in Equation~\ref{eq:ekf:z}), the predicted measurement ($\tilde{z}$) used in the update step of the EKF framework is formulated in Equation~\ref{eq:ekf:zpred}.
\begin{equation}\label{eq:ekf:h}
\tilde{p}_{b,i} = R^T \left( p_{b,i} - t \right)
\end{equation}
\begin{equation}\label{eq:ekf:z}
z=\begin{bmatrix}
d_{b,i}\\
\theta_{b,i}
\end{bmatrix}
\end{equation}
\begin{equation}\label{eq:ekf:zpred}
\tilde{z} = \begin{bmatrix}
\Vert \tilde{p}_{b,i} \Vert \\
\text{atan2}\left(\tilde{p}.y_{b,i},\tilde{p}.x_{b,i}\right)
\end{bmatrix}
\end{equation}

\begin{figure}[!t]
\centering
\centerline{}
\caption{Beacon-based Extended Kalman Filter~(EKF).}
\label{fig:localisation}
\end{figure}

\subsection{Autonomous navigation}

In the context of the Robot@Factory competition, the autonomous navigation problem can be decomposed into path planning and motion control.
Let the map representation be defined by a bi-directional graph $\mathcal{M}$ with a set of vertices $v=\{v_0,\dots,v_{j},\dots,v_{65}\}$ and a set of bi-directional edges $e=\{e_{0,1},\dots,e_{j_1,j_2},\dots,e_{26,65}\}$.
All the vertices are defined by a set of Cartesian coordinates in the global reference frame and an ID, such that $v_j=(x_j,y_j)^T$, where $j$ is the vertex ID.
For the competition, the criteria for choosing the vertices was to assign a vertex to the centre of every ArUco and keep its ID.
This option synergises with a vision-based state estimation scheme due to the fact that vertices and ArUcos share IDs, in the case of the system also using camera information for the pose estimation of the robot.
The edges were selected manually by connecting all the vertices close to each other, also taking into account the walls of the machines and warehouses on the shoop floor.
A visualisation of the graph concerning the map can be seen in Figure~\ref{fig:navigation:graph}.

\begin{figure}[!t]
\centering
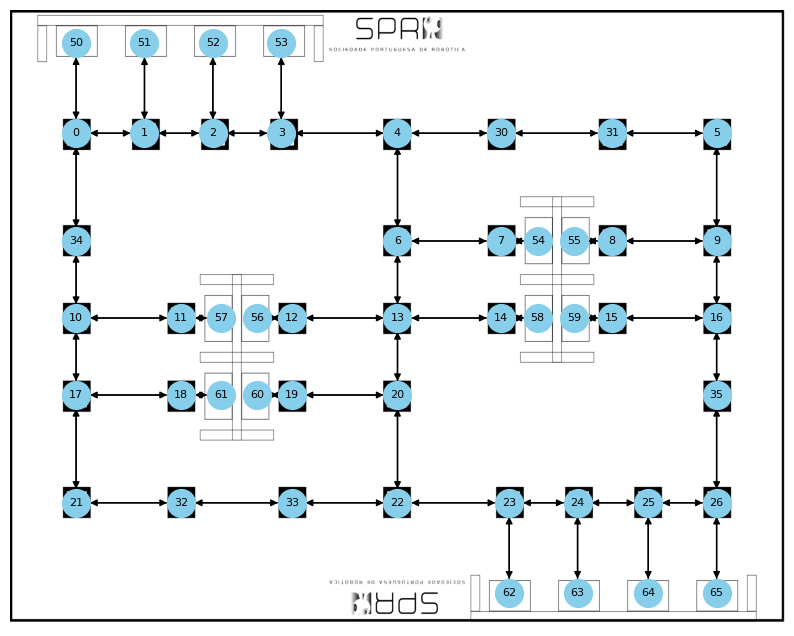
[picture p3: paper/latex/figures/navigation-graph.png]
\centerline{}
\caption{Graph-based map representation of the shop floor.}
\label{fig:navigation:graph}
\end{figure}

The path planning problem is solved in this paper by using the Dijkstra graph-search algorithm~\cite{dijkstra} to find the shortest path. The starting point of the trajectory considered in the algorithm is always the vertex closest to the robot's current pose.
Then, the path planner generates the array of edges that the robot must traverse to reach its desired goal.
As for the motion control, this paper implements a line follower algorithm based on a Proportional-Integrative-Derivative~(PID) control schema to set the linear and angular reference velocities of the omnidirectional platform.
The edges from the path planner are represented as direct lines between the affected vertices of each edge.
Moreover, the error of the PID controller to set the linear velocities is formulated as the distance of the robot's current pose to the closest point in the line.
In the case of the orientation, the error is the difference between the current heading of the robot and the orientation of the last line.
This formulation is possibly due to the decoupling property between linear and angular velocity for omnidirectional robots, allowing the independent control of linear and angular velocities.

\subsection{Human-Machine Interface (HMI)}

Finally, the HMI is based on the rviz ROS visualisation tool.
First, a pre-configuration of the rviz is automatically loaded upon launching the system framework to allow the visualisation of the
ground-truth position of the beacons,
the point cloud of the 2D laser scanner,
and the robot and world coordinate frames.
Additionally, a rviz plugin was developed to add a panel to rviz, in order to allow the user to force the start of the round without requiring the communication with the UDP server handled by the competition organisers.
Lastly, the system framework also added the possibility of launching the map\_server ROS node to visualise the same shop floor shown in Figure~\ref{fig:ratf:track-2023} in rviz with the appropriate scale, to match the remaining visual data already present in rviz.

\section{Tests and Results}\label{sec:tests}

The main result of this paper is the open-source system framework available in a public GitHub repository\footref{note:repo}.
This framework includes documentation, designs, and code implementation on all the hardware, firmware, and software that led the 5dpo Robotics team to win two consecutive editions of the Robot@Factory~4.0 competition, namely, the 2022 and 2023 editions.
The framework can be used by any future participant in the competition as a development base to allow the teams to develop their own frameworks even further and study and research more advanced techniques in sensor fusion, navigation, localisation, and motion planning.
In addition to that, educators can also use this framework to foster their students' STEM education by using project-oriented learning to introduce topics related to autonomous mobile robots.

Table~\ref{tab:results:ratf} presents the final classification results for the 2022 and 2023 editions.
The table includes the three criteria mentioned in Section~\ref{sec:ratf} to rank the teams in the Robot@Factory~4.0 competition.
Although the team accomplished the same points in both editions, there is a noticeable improvement in the time taken to finish each of the three rounds of the competition, more specifically, less than half the time.
This improvement is primarily due to improved motion planning and control algorithms in the 2023 edition and the consideration of IMU data to improve the odometry estimation of the robot and, consequently, the robot's pose estimation.
The improved motion control and planning is the consideration of a graph structure in the 2023 edition, instead of a pre-defined path, and also the fact that the robot leverages the decoupling of the linear and angular velocities to rotate along the way instead of performing on-the-spot rotations.
As for the IMU, the sensor was not present in 2022, not allowing an increase in the maximum linear and angular velocities of the robot to perform the rounds faster. Note that higher velocities increase the probability of wheel slippage occurring, worsening the wheeled odometry estimation of the robot~\cite{5dpo:sousa-2022}.

\input{tables/results}

Another improvement in the 2023 edition is using the ROS framework itself.
In 2022, the software part was based on a monolithic application based in Lazarus to provide a graphical user interface to the user of the system framework, even though implementing similar methodologies to the ones presented in this paper.
The transition to C++ and ROS-based software in the 2023 participation brought the modularity inherent to separating the different modules (e.g., the EKF localiser, odometry estimation, and motion control and planning) into independent nodes, improving the maintainability and reusability of the framework by the community.

Lastly, there are videos publicly available in YouTube to show the execution of the system framework proposed in this paper. The videos include the participation in the Robot@Factory~4.0 2022\footnote{\href{https://www.youtube.com/playlist?list=PLvp8fJUEPxYR13wTYem5suJp8_--02_mJ}{https://www.youtube.com/playlist?list=PLvp8fJUEPxYR13wTYem5suJ\\p8{-}{-}02\_mJ}} and 2023\footnote{\href{https://www.youtube.com/playlist?list=PLvp8fJUEPxYT8sAByXptjetaSgl28VxxH}{https://www.youtube.com/playlist?list=PLvp8fJUEPxYT8sAByXptjetaS\\gl28VxxH}} editions.

\section{Conclusions and Future Work}\label{sec:conclusions}

In conclusion, the system framework proposed in this paper is modular and open-source to let future participants in the Robot@Factory~4.0 competition use it as their development base.
The framework modularity allows the users to modify individual modules without interfering with other ones. The public GitHub repository\footref{note:repo} has the hardware documentation and designs (including the 3D models of the robot's parts), the firmware implementation for the Arduino Mega 2560, and the ROS-based software developed in the scope of the competition, facilitating the reuse of the system framework.
Furthermore, the framework proposed in this paper may be used for academic purposes to promote the STEM education of students with a project-oriented learning approach to introduce basic robotics concepts.
As future work, the ROS~2 compatibility will be implemented for the system framework, added camera support to detect the ArUco markers and use them in the update step of the EKF localiser, and the elaboration of a STEM education activity will be considered with even further documentation and more class-oriented contents.

\section*{Acknowledgment}

In the name of the 5dpo Robotics team, the authors thank the Electrical and Computers Engineering Department~(DEEC) from the Faculty of Engineering, University of Porto~(FEUP), the faculty itself, and the INESC TEC -- Institute for Systems and Computer Engineering, Technology and Science for all their support and assistance in the development of this work.

%%%%%%%%%%%%%%%%%%%%%%
%%%%% REFERENCES %%%%%
%%%%%%%%%%%%%%%%%%%%%%

\printbibliography

\end{document}

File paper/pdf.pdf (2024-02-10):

# System Framework for the Robot@Factory 4.0 Competition

Ricardo B. Sousa∗† | , Claudia D. Rocha ´
†‡ | , Joao G. Martins ˜
∗† | , Joao Pedro Costa ˜

∗
,
Joao Tom ˜ | as Padr ´ | ao˜

∗
, Jose Maria Sarmento ´
†‡ | , Jose Pedro Carvalho ´
∗§ | , Maria S. Lopes∗†
,
Paulo G. Costa∗† , Antonio Paulo Moreira ´

∗†
| | ∗Faculty of Engineering, University of Porto (FEUP), 4200-465 Porto, Portugal

Email: up{201503004,201806222,201806431,202108766,201806775}@edu.fe.up.pt {jpcarvalho,paco,amoreira}@fe.up.pt
†CRIIS – Centre for Robotics in Industry and Intelligent Systems INESC TEC – Institute for Systems and Computer Engineering, Technology and Science, 4200-465 Porto, Portugal
| | Email: {claudia.d.rocha,jose.m.sarmento}@inesctec.pt
‡School of Science and Technology University of Tras-os-Montes and Alto Douro (UTAD), 5000-801 Vila Real, Portugal ´ §C2SR – Cyber-Physical Control Systems and Robotics SYSTEC – Research Center for Systems and Technologies, 4200-465 Porto, Portugal

Abstract—Robotic competitions stand as platforms to propel the forefront of robotics research while nurturing STEM education, serving as hubs of both applied research and scientific innovation. In Portugal, the Portuguese Robotics Open (FNR) is a national event with several robotic competitions, including the Robot@Factory 4.0 competition. This competition presents an example of deploying autonomous robots on a factory shop floor. Although the literature has works proposing system frameworks for the original version of the Robot@Factory competition, none of them proposes a system framework for the Robot@Factory 4.0 version that presents the hardware, firmware, and software to complete the competition and achieve autonomous navigation. So, this paper proposes a complete system framework for the Robot@Factory 4.0 competition that is modular and open-access, enabling future participants to use and improve it in future editions. This work is the culmination of all the knowledge acquired by winning two editions of the competition.
Index Terms—autonomous mobile robots, robot competitions, robot at factory 4.0
I. INTRODUCTION
Since 1997, the RoboCup¹
federation has organised international robot soccer competitions, including Small and Middle Size League (SSL and MSL, respectively) robots and humanoids, and more recently, competitions focused on service (RoboCup@Home) and industrial (RoboCup@Work) autonomous robots. Another example is the Formula Student² competition, which has been held in Europe since 1999. This event includes several categories (combustion, electric, hybrid, and driverless autonomous systems) while being an educational engineering platform in several fields, such as robotics, computer science, mechanical, and electrical and

This work is financed by National Funds through the Portuguese funding
agency, FCT – Fundac¸ao para a Ci ˜ | encia e a Tecnologia, within project ˆ
LA/P/0063/2020 (DOI: 10.54499/LA/P/0063/2020). (https://doi.org/10.54499/LA/P/0063/2020) 1https://www.robocup.org/
2https://www.imeche.org/events/formula-student

computer engineering. More recently, the F1TENTH [1] and the Indy Autonomous Challenge (IAC) [2] were created to push further the research on autonomous systems and also serve as STEM education platforms for students.
In Portugal, the Portuguese Robotics Open (FNR)³
is an
event hosting several competitions divided into major and junior categories. These competitions include qualification events to decide the Portuguese teams participating in the RoboCup, international championships, autonomous driving, dragster, and the Robot@Factory Lite and Robot@Factory 4.0 competitions, which are more oriented to industrial cases. In particular, the Robot@Factory 4.0 competition aims to represent the deployment of autonomous mobile robots on a factory shop floor. The robots should be able to transport materials between warehouses or machines that process those materials, considering the robots’ ability to self-localise and navigate in order to avoid collisions with the walls.
The current literature has works oriented toward the original and present versions of the Robot@Factory competition hosted at FNR (Robot@Factory and Robot@Factory 4.0, respectively). Ribeiro et. al. [3] presented their design and development path towards the robot used to participate in the original version of the competition. The robot was a three-wheeled omnidirectional robot with five processing units (including a Raspberry Pi 2 Model B and two Arduino Mini), a 2D laser scanner, and an Inertial Measurement Unit (IMU) used to obtain a pose estimation. Similarly, Pinto et. al. [4] also proposed a three-wheeled omnidirectional robot to participate in the original competition. The proposed framework used wheeled odometry and 2D laser data to estimate the robot pose with the PerfectMatch [5] algorithm, while only using a single processing unit, namely, a Raspberry Pi 3.

3https://www.festivalnacionalrobotica.pt/

Finally, Braun et. al. [6] presented the development of a four-wheeled mecanum platform specifically designed for the Robot@Factory 4.0 competition, with a Raspberry Pi 4 and an Arduino Mega 2560 as processing units. This work focused on the mechanical design and electronics of the robot, including the description of the sensory perception system composed by a camera and a 2D laser scanner. In conclusion, the works of Ribeiro et. al. [3] and Pinto et. al. [4] are not intended for the present version of the Robot@Factory competition, while the work of Braun et. al. [6] does not cover the software architecture and implementation part of the robot.
Thus, this paper proposes a modular and open-access system framework for an autonomous robot to be able to participate in future editions of the Robot@Factory 4.0 competition. The description of the proposed framework includes the hardware, firmware, and software implemented by the 5dpo Robotics Team⁴
that led the team to win two consecutive editions of the competition. All the code relative to firmware and software developed within the context of the competition, 3D models of the robot parts, and additional documentation are available in a public GitHub repository⁵
. Indeed, this repository containing the implementation of the proposed framework may be used by future participants in the competition to have an initial start on their development and push it even further to foster their STEM education knowledge. To the best of the authors’ knowledge, and according to the related works information found in the literature, no framework encompasses hardware, software, and system integration to allow building an entire robot system for the Robot@Factory 4.0 competition.
The remaining of this paper is organised as follows. Section II presents a brief summary of the current version of the Robot@Factory 4.0 competition. Section III describes the architecture of the proposed system framework. Then, Sections IV, V, and VI characterise the hardware, firmware, and software implemented and used in the competition, respectively. Section VII presents the results originated from the participation in two editions of Robot@Factory 4.0. Lastly, Section VIII formulates the final conclusions and future work.

II. ROBOT@FACTORY 4.0 COMPETITION

The competition presents the problem of deploying autonomous mobile robots on a factory shop floor (illustrated in Figure 1). One or more robots should transport materials between warehouses or machines, depending on the type of materials received in the input warehouse. The robots will transport three different parts from the incoming warehouse: blue, green, and red boxes. The first is considered a final part; thus, it is sent directly to the output warehouse. The second one is an intermediate part that must receive a transformation to a blue box at either machines A or B. Lastly, the red box must suffer two transformations, first on machine A to a green part, and then on B to a blue box. Furthermore, the competition is divided into three rounds. The rounds are distinguished by the

4https://5dpo.github.io/
5https://github.com/5dpo/5dpo ratf 2023 (https://github.com/5dpo/5dpo_ratf_2023)

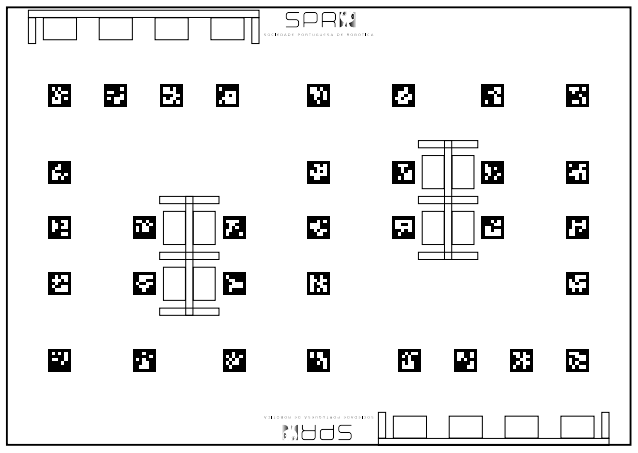
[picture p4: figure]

Fig. 1: Shop floor of the Robot@Factory 4.0 2023 edition composed by warehouses (input on the top-left and output on the bottom-right of the floor), machines (middle wall markings, where the machines A are on the left and B on the right side), and ArUco markers [7].

type of parts received in the incoming warehouse: only blue parts are considered in the first round, in the second one may exist some green parts (usually, two boxes), and in the third round may have both green and red parts (usually, two and one boxes, respectively). The robot must communicate with a Wi-Fi server to get which part types are available for each slot in the incoming warehouse at the start of each run.
As for the robot design, each robot must fit into a 30×30 cm rectangle with a maximum height of 30 cm. The robot must be completely autonomous and cannot communication with any type of external systems that are not provided by the organisation. Unlike the original version of the Robot@Factory competition, the shop floor has no guiding lines nor outer walls delimiting the shop floor area. The teams can use the ArUco markers on the floor for localisation (the guidelines of the competition available in [7] present the ground-truth position of those). Additionally, the teams can place their own markers (e.g., reflectors or poles) near the corners of the factory, providing that these do not exceed an occupied area of 10 × 10 cm and a maximum height of 50 cm.
In terms of the final classification, the team with the highest total number of parts correctly transported to the outgoing warehouse or to a machine is the winner. In case of teams with the same total number of points, the first criteria is the number of correctly places parts in the outgoing warehouse, and the second criteria is the shortest time to finish the round.

III. SYSTEM ARCHITECTURE
The system framework proposed in this paper and illustrated in Figure 2 is composed of three elements: all the components and mechanics related to the robot (motors, sensors, actuators), the firmware layer to interact with low-level devices (including motors speed reading and control) running in an Arduino Mega 2560, and the software executing in a Raspberry Pi 4B 4G (drivers to interact with the firmware and other devices, localisation and navigation modules). First, the

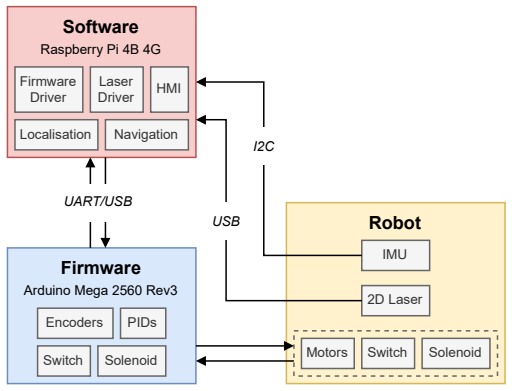
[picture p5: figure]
Robot; Firmware; Arduino Mega 2560 Rev3; Encoders; PIDs; Switch; Solenoid; Software; Raspberry Pi 4B 4G; Firmware Driver; Laser Driver; HMI; Localisation; Navigation; UART/USB; 2D Laser; Motors; IMU; USB

Fig. 2: System architecture proposed in this paper for the Robot@Factory 4.0 competition.

robot is a four-wheeled omnidirectional platform designed in the scope of the Robot@Factory 4.0 competition, using a 3D printer to make the parts of the platform. The robot includes a switch and a solenoid to sense and transport the boxes. Next, the firmware layer controls the motors’ angular speed, counts the encoder quadrature pulses, reads the switch state, and actuates the solenoid according to the software. Then, the software executes Robot Operating System (ROS) nodes implemented in C++ to interact with the firmware and other devices (including the 2D laser scanner), estimate the robot pose, provide a Human-Machine Interface (HMI) interface based on rviz, and enable the autonomous navigation of the robot to execute the desired tasks. The following sections explain each element of the system framework in depth.

IV. HARDWARE

A. Robot motion

In terms of the robot motion, the four-wheeled omnidirectional platform designed in the scope of the competition is illustrated in Figure 3. This platform uses 60 mm aluminium mecanum wheels, where the distance between the front-back and left-right wheels is 0.152 m and 0.193 m, respectively. As a consequence of using four mecanum wheels, the robot has holonomic kinematics, originating that the robot’s linear and angular velocities are decoupled from each other (e.g., the robot can manoeuvre around obstacles without affecting the orientation) [8]. Indeed, this design choice results in an increased flexibility in terms of path planning and trajectory control, where the robot may rotate along the trajectory without requiring to do on-the-spot rotations.
Furthermore, the motors chosen are 12V DC motors with 251 rpm at no load from DFRobot. The motors include a 43.7:1 metal gearbox and integrated quadrature encoders based on the Hall effect. These encoders have a resolution of 16 counts per revolution of the motor shaft, resulting in approximately 700 counts of the gearbox’s output shaft. If the firmware can process the pulses, this setup results in a resolution of 2800 pulses per revolution on the robot’s wheels.


(a)


(b)

Fig. 3: Four-wheeled omnidirectional platform designed in the scope of the competition: (a) the robot; (b) the bottom with the suspension.

An additional design constraint must be accounted for because the robot has four wheels. Conventionally, the static stability of a robot requires a minimum of three wheels, where the triangle formed by the ground contact points must contain the centre of gravity. The latter is ensured in the proposed platform by most of the components being in the volume between the front and back wheels. However, once the number of contact points exceeds three, the geometry requires some form of flexible suspension on uneven terrain [8]. Even though the floor of the competition should be flat and even, Figure 3b shows the suspension put in the robot to be compatible with terrain with minor imperfections in terms of its flatness.

B. Processing unit

Next, an Arduino Mega 2560 executes the firmware described in this paper. This microcontroller board is compatible with several open-source libraries, including the SPI⁶ (communication with SPI devices) and TimerOne & TimerThree⁷ (implementation of timers with PWM pins) libraries used in this work. Moreover, the 5V operating voltage of the

6https://www.arduino.cc/reference/en/language/functions/communication/spi/ (https://www.arduino.cc/reference/en/language/functions/communication/spi/)
7https://www.pjrc.com/teensy/td libs TimerOne.html (https://www.pjrc.com/teensy/td_libs_TimerOne.html)

Arduino Mega is directly compatible with the voltage of the encoders of the motors and the electromagnet actuation.
As for the software, the Raspberry Pi 4B 4GB executes all the ROS nodes implemented in C++. Given that this paper uses ROS 1 Noetic, the Operating System (OS) running in the Raspberry Pi was the Raspberry OS (Legacy) based on Debian Buster. However, the OS Ubuntu 20.04 may also be used instead of Raspbian, in case there is no need for graphical output. Also, the advantages of using Raspberry Pi are its compatibility with the Raspberry Pi Camera module (e.g., for ArUco markers detection) and its 40 General-Purpose Input/Output (GPIO) pins compatible with SPI and I2C devices.
C. Sensors
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

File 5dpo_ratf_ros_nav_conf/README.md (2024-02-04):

# [5dpo_ratf_ros_nav_conf](https://github.com/5dpo/5dpo_ratf_ros_nav_conf)

**Version 0.2.4**

This repository implements the launch files required for the 5DPO Navigation
Stack on the four-wheeled omnidirectional robotic platform used by the
[5dpo FEUP Robotics Team](https://github.com/5dpo) in the
[Robot@Factory](https://www.festivalnacionalrobotica.pt/) competition. The
system implemented is based on the INESC TEC Robotics Navigation Stack that it
allows you to have different configurations implemented and selecting just one
based on your environment variables.

**With this version, it is possible to do:**

- ROS package creation (`CMakeLists.txt`, `package.xml`)
- `basic` configuration
- `ratf2023` configuration

**The next version will add these features:**

- TBD
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

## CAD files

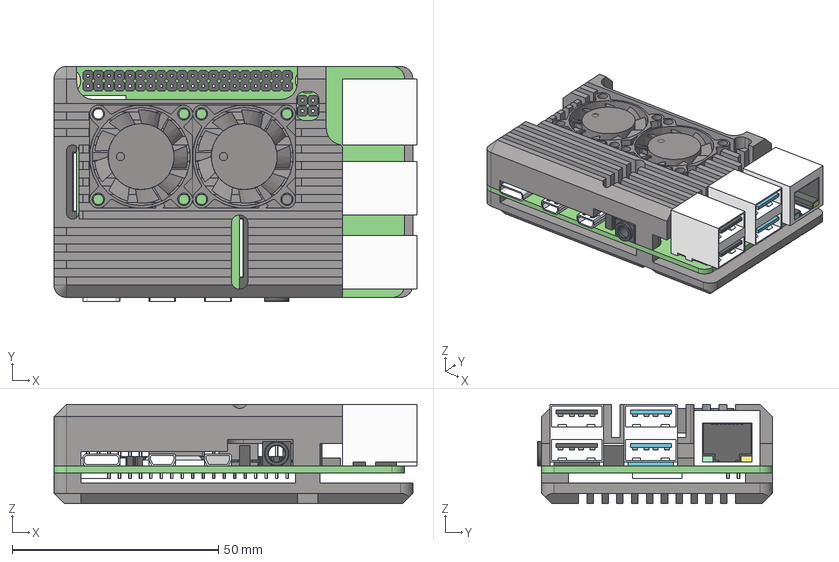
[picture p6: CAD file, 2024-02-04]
cad/full+raspberry+pi+4+upgrade+cooling.stp
88.0 x 57.0 x 24.1 mm
радиатор верх v21
радиатор низ v4
вентилятор v6 x 2

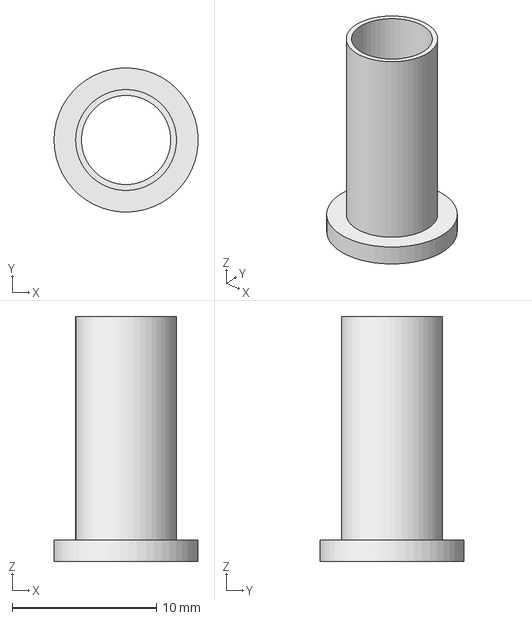
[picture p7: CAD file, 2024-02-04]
cad/Anilha.stp
9.99 x 10.00 x 17.0 mm

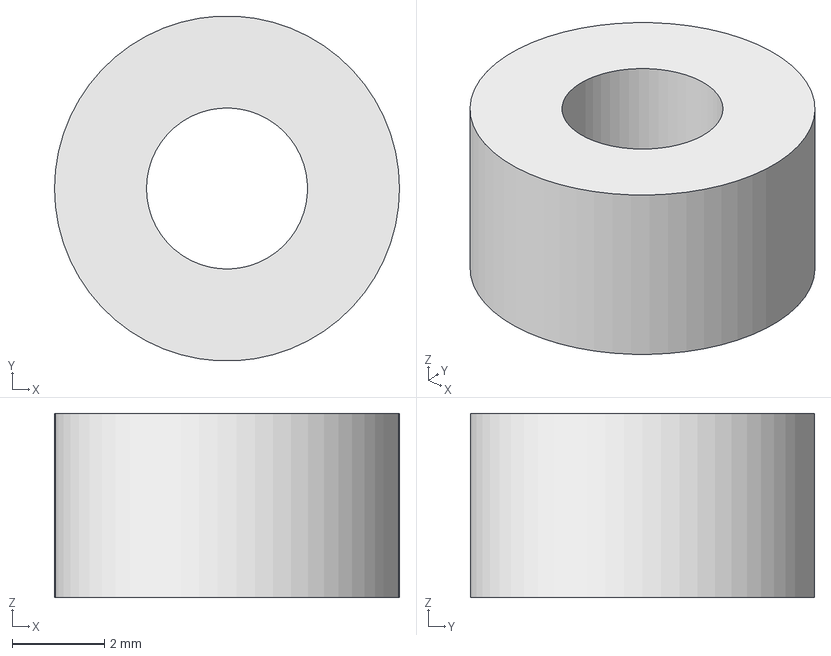
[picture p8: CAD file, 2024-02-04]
cad/Anilha_4.stp
7.50 x 7.49 x 4.00 mm

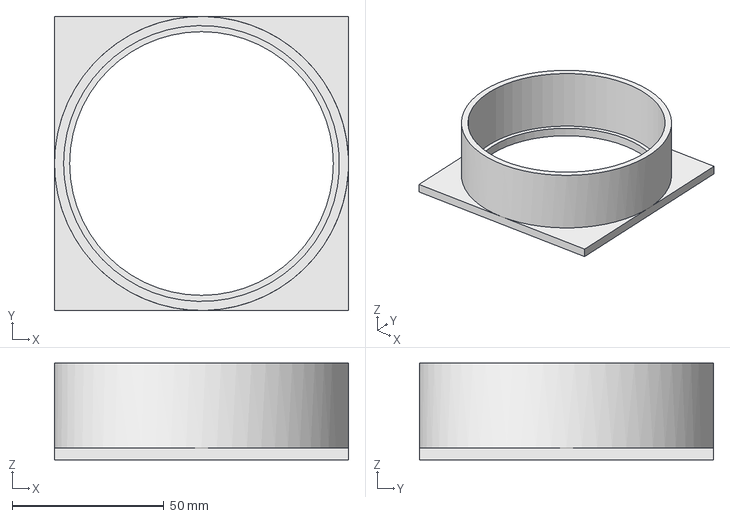
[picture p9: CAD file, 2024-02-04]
cad/Suporte_postes.stp
97.0 x 97.0 x 32.0 mm

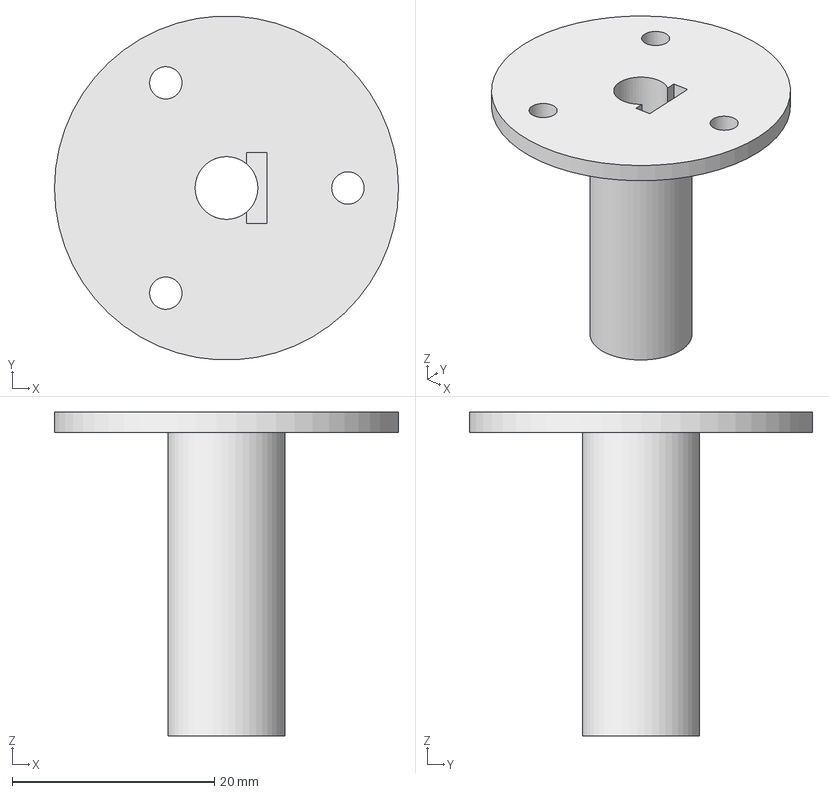
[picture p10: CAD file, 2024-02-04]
cad/eixo_roda.stp
34.0 x 33.9 x 32.0 mm

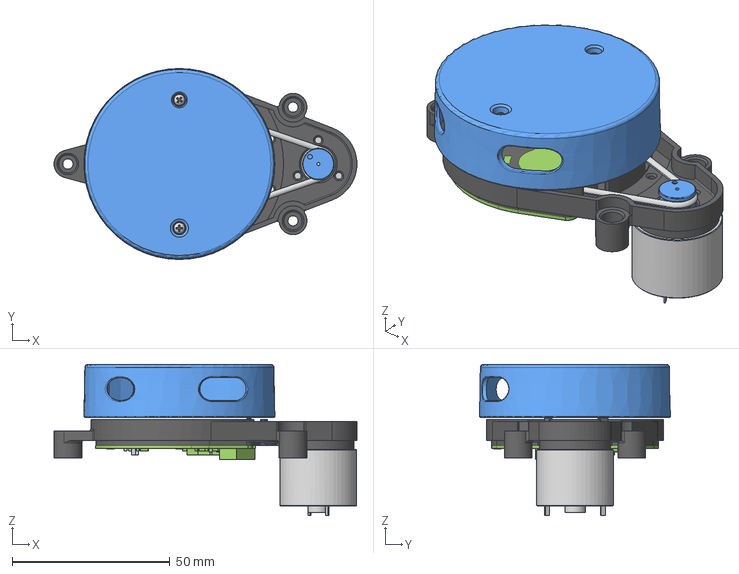
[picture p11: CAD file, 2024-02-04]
cad/ydliar_X2.stp
95.9 x 60.5 x 48.0 mm

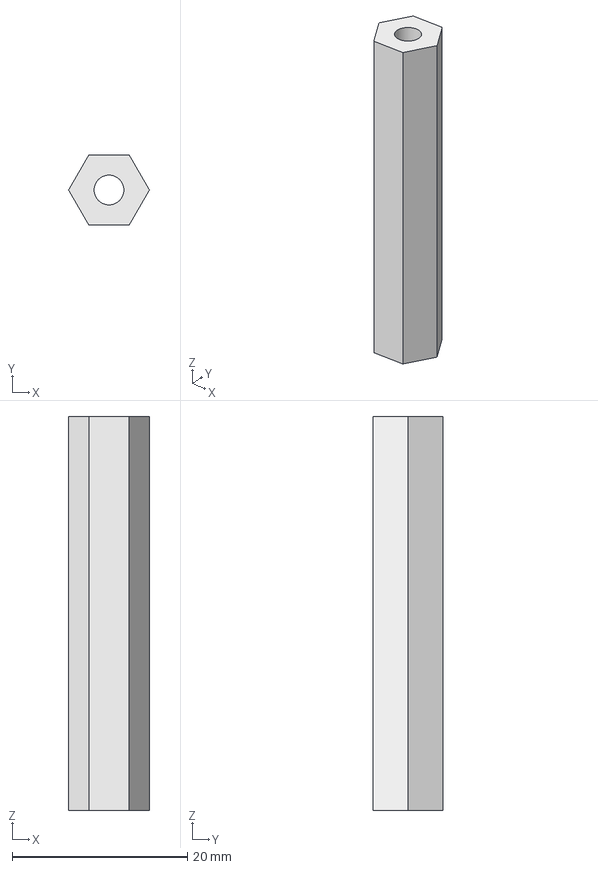
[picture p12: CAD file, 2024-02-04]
cad/pillar.stp
9.24 x 8.00 x 45.0 mm

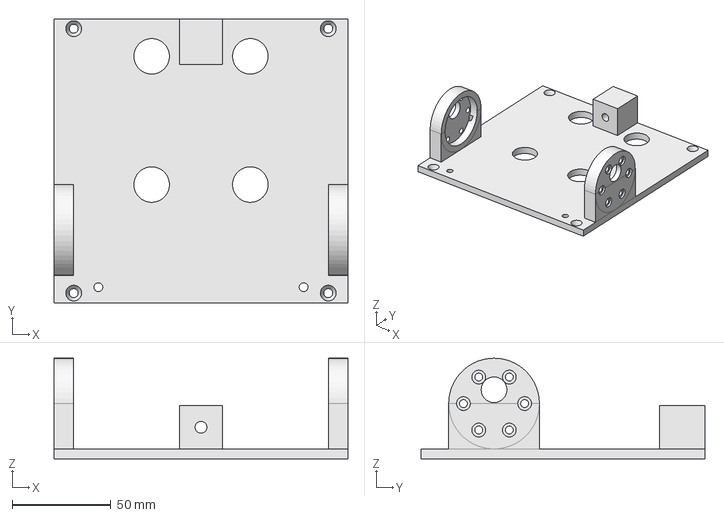
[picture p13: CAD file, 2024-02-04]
cad/Estrutura_robo.stp
149.0 x 143.9 x 51.0 mm

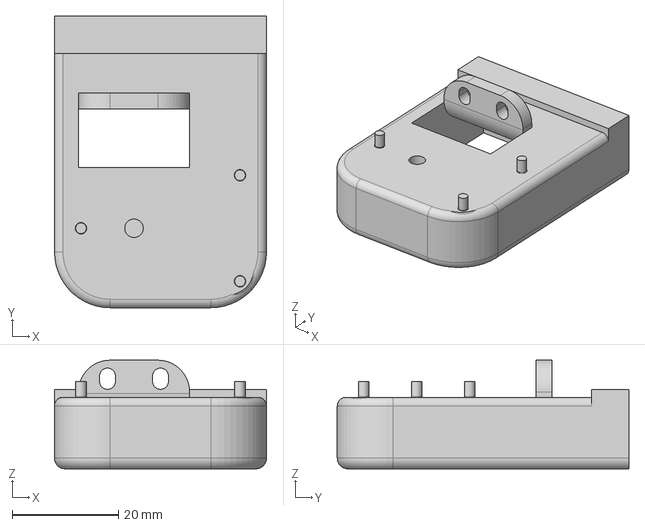
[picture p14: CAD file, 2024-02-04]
cad/Eletro_Iman_support+v2.stp
40.0 x 55.0 x 20.5 mm

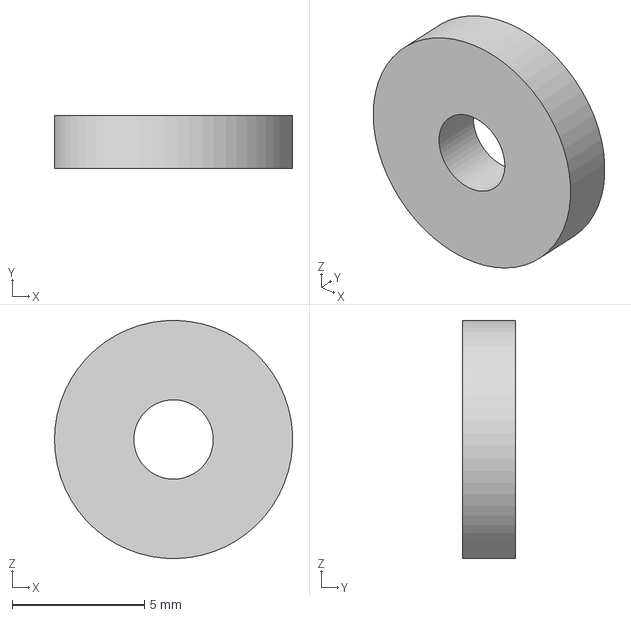
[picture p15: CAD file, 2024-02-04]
cad/anilhaimu.stp
8.99 x 2.00 x 9.00 mm

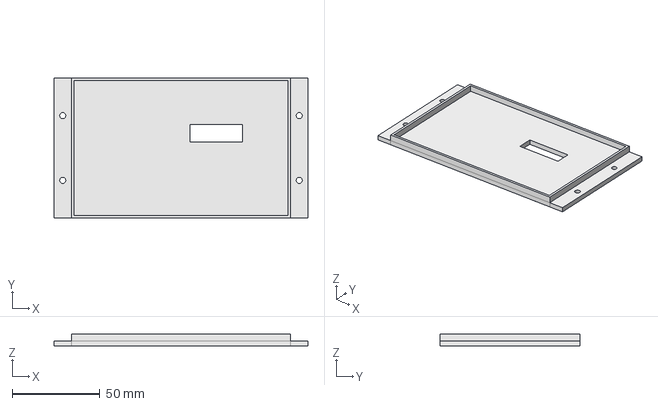
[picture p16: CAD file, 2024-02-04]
cad/LCD_frame.stp
145.0 x 80.0 x 7.00 mm

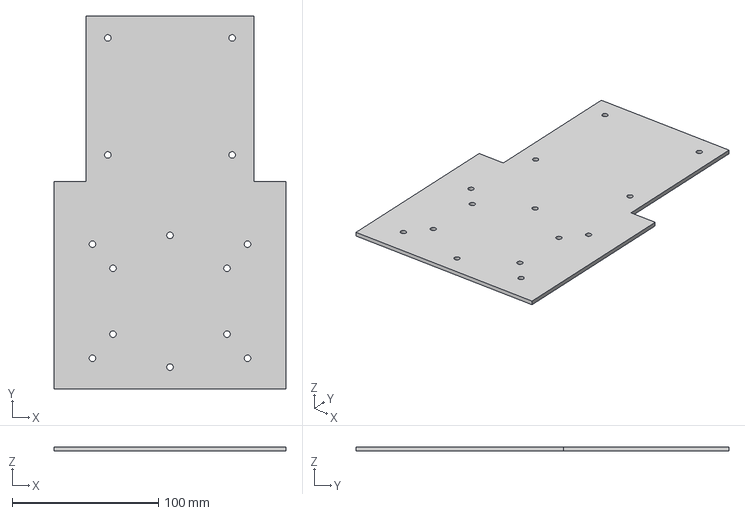
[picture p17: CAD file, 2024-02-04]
cad/chapa_v6.stp
158.6 x 255.0 x 3.00 mm

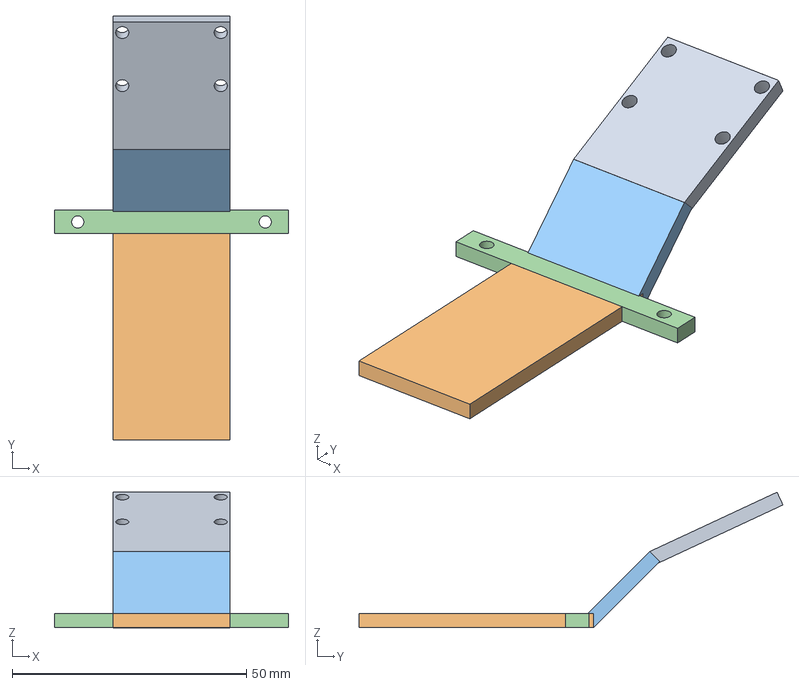
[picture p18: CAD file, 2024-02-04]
cad/suporte_camara.stp
50.0 x 90.4 x 28.9 mm

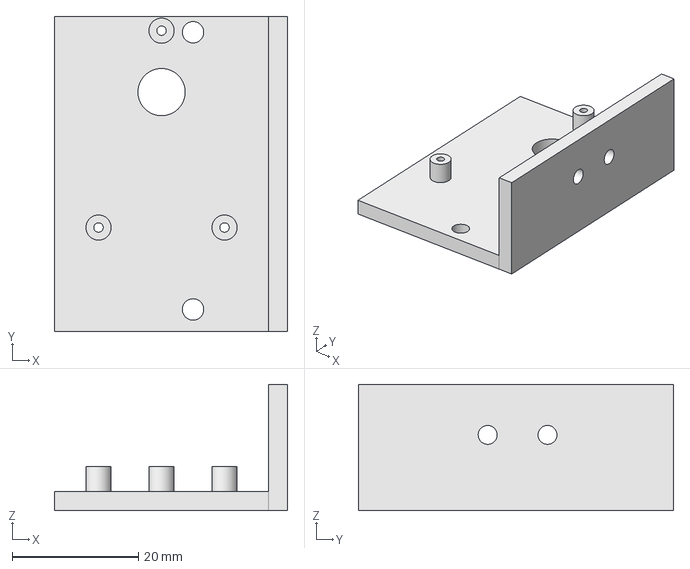
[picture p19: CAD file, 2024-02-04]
cad/suporte_eletroiman.stp
37.0 x 50.0 x 20.0 mm

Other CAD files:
cad/Modular_design.stp
cad/placa_sup_rasp.stp
cad/suporte_bateria_FOmni.stp
cad/suporte_eletroiman_interno.stp
cad/Cam+V2.stp
cad/Eletro_Iman_support+v1.stp
cad/Estrutura_robo_superior.stp
cad/Fixed.stp
cad/Suportes_laser.stp
cad/ydlidar x4.SLDPRT

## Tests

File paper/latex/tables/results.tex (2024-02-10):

\begin{table}[t!]

\centering
\caption{Final Classification Results of the 5dpo Robotics Team in the Robot@Factory~4.0 2022 and 2023 Editions.}
\label{tab:results:ratf}

\begin{tabular}{l c c c c c}

%% HEADER
\hline
\textbf{Edition} &
\textbf{Round} &
\textbf{Place} &
\textbf{\#total} &
\textbf{\#outgoing} &
\textbf{Time} (s)\\
\hline

%% TABLE CONTENTS
2022 &                  % edition
1\textsuperscript{st} & % round
1\textsuperscript{st} & % place
4                     & % #total
4                     & % #outgoing
124\\
 &                      % edition
2\textsuperscript{nd} & % round
1\textsuperscript{st} & % place
6                     & % #total
4                     & % #outgoing
126\\
 &                      % edition
3\textsuperscript{rd} & % round
1\textsuperscript{st} & % place
8                     & % #total
4                     & % #outgoing
134\\
\hline
2023 &                  % edition
1\textsuperscript{st} & % round
1\textsuperscript{st} & % place
4                     & % #total
4                     & % #outgoing
40.7\\
 &                      % edition
2\textsuperscript{nd} & % round
1\textsuperscript{st} & % place
6                     & % #total
4                     & % #outgoing
47.3\\
 &                      % edition
3\textsuperscript{rd} & % round
1\textsuperscript{st} & % place
8                     & % #total
4                     & % #outgoing
60.9\\
\hline

\end{tabular}

\end{table}

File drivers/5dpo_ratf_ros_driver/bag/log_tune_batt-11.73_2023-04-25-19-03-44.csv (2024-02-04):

secs | nsecs | sample_period | pwm | encoder_delta | ticks_per_rev | angular_speed | sample_period | pwm | encoder_delta | ticks_per_rev | angular_speed | sample_period | pwm | encoder_delta | ticks_per_rev | angular_speed | sample_period | pwm | encoder_delta | ticks_per_rev | angular_speed
1682445825 | 670712378 | 0.020024 | 0 | 0 | 2803.2 | 0 | 0.020024 | 0 | 0 | 2803.2 | 0 | 0.020024 | 0 | 0 | 2803.2 | 0 | 0.020024 | 0 | 117 | 2803.2 | 13.11238372
1682445825 | 691227086 | 0.02002 | 0 | -1098 | 2803.2 | -123.054678 | 0.02002 | 0 | 64 | 2803.2 | 7.172585967 | 0.02002 | 0 | -3307 | 2803.2 | -370.6209655 | 0.02002 | 0 | -2303 | 2803.2 | -258.1010232
1682445825 | 711708331 | 0.020024 | 0 | 0 | 2803.2 | 0 | 0.020024 | 0 | 0 | 2803.2 | 0 | 0.020024 | 0 | 0 | 2803.2 | 0 | 0.020024 | 0 | 0 | 2803.2 | 0
1682445825 | 732246816 | 0.020016 | 0 | 0 | 2803.2 | 0 | 0.020016 | 0 | 0 | 2803.2 | 0 | 0.020016 | 0 | 0 | 2803.2 | 0 | 0.020016 | 0 | 0 | 2803.2 | 0
1682445825 | 752758802 | 0.020004 | 0 | 0 | 2803.2 | 0 | 0.020004 | 0 | 0 | 2803.2 | 0 | 0.020004 | 0 | 0 | 2803.2 | 0 | 0.020004 | 0 | 0 | 2803.2 | 0
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

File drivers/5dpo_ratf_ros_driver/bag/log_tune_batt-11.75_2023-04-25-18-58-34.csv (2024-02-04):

secs | nsecs | sample_period | pwm | encoder_delta | ticks_per_rev | angular_speed | sample_period | pwm | encoder_delta | ticks_per_rev | angular_speed | sample_period | pwm | encoder_delta | ticks_per_rev | angular_speed | sample_period | pwm | encoder_delta | ticks_per_rev | angular_speed
1682445515 | 465702121 | 0 | 0 | 0 | 2803.2 | 0 | 0 | 0 | 0 | 2803.2 | 0 | 0 | 0 | 0 | 2803.2 | 0 | 0 | 0 | 0 | 2803.2 | 0
1682445515 | 486207588 | 0.02002 | 0 | 0 | 2803.2 | 0 | 0.02002 | 0 | 0 | 2803.2 | 0 | 0.02002 | 0 | 0 | 2803.2 | 0 | 0.02002 | 0 | 0 | 2803.2 | 0
1682445515 | 506690889 | 0.02002 | 0 | 0 | 2803.2 | 0 | 0.02002 | 0 | 0 | 2803.2 | 0 | 0.02002 | 0 | 0 | 2803.2 | 0 | 0.02002 | 0 | 0 | 2803.2 | 0
1682445515 | 527240374 | 0.020004 | 0 | 0 | 2803.2 | 0 | 0.020004 | 0 | 0 | 2803.2 | 0 | 0.020004 | 0 | 0 | 2803.2 | 0 | 0.020004 | 0 | 0 | 2803.2 | 0
1682445515 | 547728971 | 0.02002 | 0 | 0 | 2803.2 | 0 | 0.02002 | 0 | 0 | 2803.2 | 0 | 0.02002 | 0 | 0 | 2803.2 | 0 | 0.02002 | 0 | 0 | 2803.2 | 0
1682445515 | 563929941 | 0.020016 | 0 | 0 | 2803.2 | 0 | 0.020016 | 0 | 0 | 2803.2 | 0 | 0.020016 | 0 | 0 | 2803.2 | 0 | 0.020016 | 0 | 0 | 2803.2 | 0
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

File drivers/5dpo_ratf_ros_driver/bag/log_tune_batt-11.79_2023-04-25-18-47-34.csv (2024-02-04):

secs | nsecs | sample_period | pwm | encoder_delta | ticks_per_rev | angular_speed | sample_period | pwm | encoder_delta | ticks_per_rev | angular_speed | sample_period | pwm | encoder_delta | ticks_per_rev | angular_speed | sample_period | pwm | encoder_delta | ticks_per_rev | angular_speed
1682444855 | 216766609 | 0 | 0 | 0 | 2803.2 | 0 | 0 | 0 | 0 | 2803.2 | 0 | 0 | 0 | 0 | 2803.2 | 0 | 0 | 0 | 0 | 2803.2 | 0
1682444855 | 237298631 | 0.02002 | 0 | 0 | 2803.2 | 0 | 0.02002 | 0 | 0 | 2803.2 | 0 | 0.02002 | 0 | 0 | 2803.2 | 0 | 0.02002 | 0 | 0 | 2803.2 | 0
1682444855 | 257769728 | 0.020024 | 0 | 0 | 2803.2 | 0 | 0.020024 | 0 | 0 | 2803.2 | 0 | 0.020024 | 0 | 0 | 2803.2 | 0 | 0.020024 | 0 | 0 | 2803.2 | 0
1682444855 | 278296362 | 0.02002 | 0 | 0 | 2803.2 | 0 | 0.02002 | 0 | 0 | 2803.2 | 0 | 0.02002 | 0 | 0 | 2803.2 | 0 | 0.02002 | 0 | 0 | 2803.2 | 0
1682444855 | 298850013 | 0.02002 | 0 | 0 | 2803.2 | 0 | 0.02002 | 0 | 0 | 2803.2 | 0 | 0.02002 | 0 | 0 | 2803.2 | 0 | 0.02002 | 0 | 0 | 2803.2 | 0
1682444855 | 319427405 | 0.020036 | 0 | 0 | 2803.2 | 0 | 0.020036 | 0 | 0 | 2803.2 | 0 | 0.020036 | 0 | 0 | 2803.2 | 0 | 0.020036 | 0 | 0 | 2803.2 | 0
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

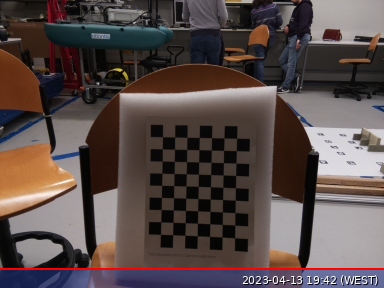
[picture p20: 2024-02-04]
drivers/5dpo_driver_ros_camera/scripts/intrinsic-calibration/206/images/image.jpg

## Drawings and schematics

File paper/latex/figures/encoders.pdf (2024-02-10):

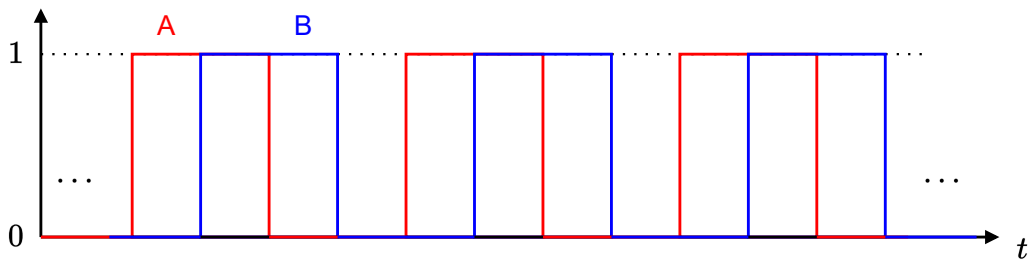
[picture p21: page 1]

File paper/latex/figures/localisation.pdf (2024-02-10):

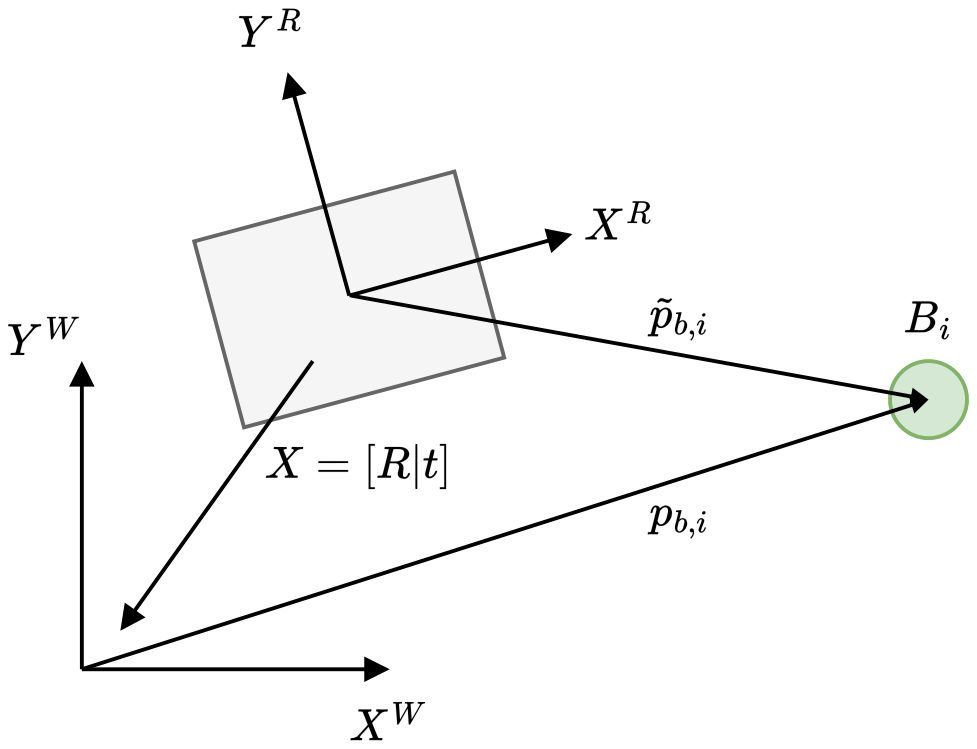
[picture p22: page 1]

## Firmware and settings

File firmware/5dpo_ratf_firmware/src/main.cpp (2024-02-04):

#include <Arduino.h>

#include <channels.h>

#include "Robot.h"

/******************************************************************************
 * GLOBAL VARIABLES
 ******************************************************************************/
Adafruit_MotorShield AFMS = Adafruit_MotorShield();

unsigned long current_micros = 0, previous_micros = 0;
unsigned long last_motor_update_millis = 0;
bool timeout = false;
channels_t serial_channels;
//uint8_t builtin_led_state;

Robot robot;
Encoder *encoders = robot.enc;



/******************************************************************************
 * FUNCTIONS HEADERS
 ******************************************************************************/
void processSerialPacket(char channel, uint32_t value, channels_t& obj);
void serialWrite(uint8_t b);
void serialWriteChannel(char channel, int32_t value);
void serialRead();
void checkMotorsTimeout();



/******************************************************************************
 * IMPLEMENTATION
 ******************************************************************************/
void setup() {
  // Built-in LED
  /*builtin_led_state = LOW;
  pinMode(LED_BUILTIN, OUTPUT);
  digitalWrite(LED_BUILTIN, builtin_led_state);*/

  // Robot
  robot.init(serialWriteChannel);

  // Serial communication
  Serial.begin(115200);
  serial_channels.init(processSerialPacket, serialWrite);

  // Reset signal
  serialWriteChannel('r', 0);

  // Test PWM motors
  /*robot.setMotorPWM(0, 0);
  robot.setMotorPWM(1, 0);
  robot.setMotorPWM(2, 0);
  robot.setMotorPWM(3, 0);*/

  // Initialization
  current_micros = micros();
  previous_micros = current_micros;
  last_motor_update_millis = millis();
}

void loop() {
  //static unsigned long blink_led_decimate = 0;
  uint32_t delta;

  serialRead();

  current_micros = micros();
  delta = current_micros - previous_micros;
  if (delta > kMotCtrlTimeUs) {
    if (kMotCtrlTimeoutEnable) {
      checkMotorsTimeout();
    }

    if (!timeout) {
      previous_micros = current_micros;
      
      // Update and send data
      robot.update(delta);
      robot.send();

      // Debug (Serial Monitor)
      //serialWrite('\n');

      // Blink LED
      /*blink_led_decimate++;
      if (blink_led_decimate >= kMotCtrlLEDOkCount) {
        if (builtin_led_state == LOW) {
          builtin_led_state = HIGH;
        } else {
          builtin_led_state = LOW;
        }
        digitalWrite(LED_BUILTIN, builtin_led_state);
        blink_led_decimate = 0;
      }*/
    }
  }
}



/******************************************************************************
 * FUNCTIONS IMPLEMENTATIONS
 ******************************************************************************/
void processSerialPacket(char channel, uint32_t value, channels_t& obj) {
  uint8_t mot_i;
  int16_t pwm;

  // Reset watchdog
  if ((channel == 'G') || (channel == 'K')) {
    last_motor_update_millis = millis();
  }

  // Process incomming serial packet
  switch (channel) {
    // - reference angular speed
    case 'G':
    case 'H':
    case 'I':
    case 'J':
      mot_i = channel - 'G';
      // set reference angular speed for the motors
#ifdef CONFIG_LAZARUS
      robot.setMotorWref(mot_i, ((int32_t) value) * kEncImp2MotW );
#endif
#ifdef CONFIG_ROS
      robot.setMotorWref(mot_i, *((float*) &value) );
#endif
      break;
  
    // - PWM
    case 'K':
      mot_i = (value >> 24) & 0x03;
      pwm = value & 0xFFFF;
      robot.setMotorPWM(mot_i, pwm);
      break;

    // - solenoid
    case 'L':
      digitalWrite(kRobotActSolenoidPin, value);
      break;
  }
}

void serialWrite(uint8_t b) {
  Serial.write(b);
}

void serialWriteChannel(char channel, int32_t value) {
  serial_channels.send(channel, value);
}

void serialRead() {
  uint8_t serial_byte;

  if (Serial.available() > 0) {
    serial_byte = Serial.read();
    serial_channels.StateMachine(serial_byte);
  }
}

void checkMotorsTimeout() {
  if (millis() - last_motor_update_millis > kMotCtrlTimeout) {
    timeout = true;

    robot.stop();
    digitalWrite(kRobotActSolenoidPin, 0);

    /*builtin_led_state = LOW;
    digitalWrite(LED_BUILTIN, builtin_led_state);*/

  } else {
    if (timeout) {
      robot.init(serialWriteChannel);
    }

    timeout = 0;
  }
}

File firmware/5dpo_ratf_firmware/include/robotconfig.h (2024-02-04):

#ifndef ROBOTCONFIG_H
#define ROBOTCONFIG_H

#include <Arduino.h>

/******************************************************************************
 * Configuration (uncomment the appropriate configuration)
 * - Lazarus-based applications (original channels implementation)
 * - ROS-based navigation stack (modified implementation of channels with the
 *     using the ROS package serial_communication_channels
 ******************************************************************************/
//#define CONFIG_LAZARUS        //!< firmware communicates to a Lazarus app
#define CONFIG_ROS            //!< firmware communicates to a ROS-based app

/******************************************************************************
 * Robot parameters
 * - kinematic configuration
 * - battery
 ******************************************************************************/
const float kRobotL[] = {     //!< robot geometric distances
  0.200,    //!< front-back wheel distance
  0.200     //!< left-right wheel distance
};
const float kRobotWhD[] = {   //!< diameter of the wheels 0-3 (m)
  0.0600,   //!< back-right wheel
  0.0600,   //!< back-left  wheel
  0.0600,   //!< front-right wheel
  0.0600    //!< front-left  wheel
};
const float kRobotBattVnom = 11.1;    //!< nominal battery level (V)

/******************************************************************************
 * General inputs / outputs
 * - solenoid
 * - switch
 ******************************************************************************/
const uint8_t kRobotActSolenoidPin = 30;
const uint8_t kRobotSensSwitchPin = 53;

/******************************************************************************
 * Motor parameters
 * - gear reduction ratio and encoders resolution
 * - controllers parameters
 ******************************************************************************/
const float kMotNgear  = 43.8;    //!< gear reduction ratio (n:1)
const float kMotEncRes = 16*4;    //!< encoder resolution (tick count per rev.)

const uint8_t kMotEncPin0A = 22;  //!< encoder channel A of back-right wheel
const uint8_t kMotEncPin0B = 23;  //!< encoder channel B of back-right wheel
const uint8_t kMotEncPin1A = 24;  //!< encoder channel A of back-left wheel
const uint8_t kMotEncPin1B = 25;  //!< encoder channel B of back-left wheel
const uint8_t kMotEncPin2A = 26;  //!< encoder channel A of front-right wheel
const uint8_t kMotEncPin2B = 27;  //!< encoder channel B of front-right wheel
const uint8_t kMotEncPin3A = 28;  //!< encoder channel A of front-left wheel
const uint8_t kMotEncPin3B = 29;  //!< encoder channel B of front-left wheel

const float kMotModelKp  = 4.5000;    //!< gain (rad.s^(-1) / V)
const float kMotModelTau = 0.1000;    //!< time constant (s)
const float kMotModelLag = 0.0000;    //!< lag lag (s)

const unsigned long kMotCtrlFreq = 50UL;      //!< frequency (Hz)
const float kMotCtrlTime = 1.0 / kMotCtrlFreq;//!< period (s)
const unsigned long kMotCtrlTimeUs = 1000000UL / kMotCtrlFreq;
const unsigned long kMotCtrlTimeout = 100UL;  //!< watchdog timeout (ms)
const bool kMotCtrlTimeoutEnable = true;      //!< enable watchdog (true/false)

const unsigned long kMotCtrlLEDOkFreq = 4UL;  //!< heartbeat LED frequency (Hz)
const unsigned long kMotCtrlLEDOkCount =
    1000000UL / kMotCtrlLEDOkFreq / kMotCtrlTimeUs / 2;

const float kMotVmax = 12;          //!< maximum voltage appliable to motors (V)
const int16_t kMotPWMmax = 255;     //!< maximum PWM (0..1023)
const int16_t kMotPWMDeltaMax = 100;//!< maximum variation in PWM (0..1023)
const bool kMotPWMDeltaMaxEnabled = true; //!< enable limits on PWM variation

const float kMotHammV0 = 0.20;         //!< estimated motors' deadzone (V)
const float kMotHammVd = 0.12;         //!< compensated motors' deadzone (V)

//! IMC tunning: desired time constant for the closed-loop (s)
const float kMotCtrlTauCl = kMotModelTau / 1.0;
//! IMC tunning: Kc_PI * Kp_plant
const float kMotCtrlKcKp = kMotModelTau / (kMotCtrlTauCl + kMotModelLag);
//! PI proportional gain (V / rad.s^(-1))
const float kMotCtrlKc = kMotCtrlKcKp / kMotModelKp;
//! PI integration time (s)
const float kMotCtrlTi = kMotModelTau;
//! Feed-Forward constant
const float kMotCtrlKf = 0.456294584;

/******************************************************************************
 * Conversion constants
 ******************************************************************************/
//! Conversion constant: encoder pulses (ticks) > motor angular speed (rad/s)
const float kEncImp2MotW =
    2 * PI * 1000000 / (1.0 * kMotCtrlTimeUs * kMotNgear * kMotEncRes);
//! Conversion constant: motor voltage (V) > PWM (0..PWM_max)
const float kMotV2MotPWM = kMotPWMmax * 1.0 / kRobotBattVnom;

#endif

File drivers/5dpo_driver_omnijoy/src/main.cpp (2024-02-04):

#include <ros/ros.h>
#include <geometry_msgs/Twist.h>
#include <sensor_msgs/Joy.h>

namespace sdpo_driver_omnijoy {

class Omnijoy {
 public:
  Omnijoy();

 private:
  void joyCallback(const sensor_msgs::Joy::ConstPtr& joy);
  void publish();

  ros::NodeHandle ph_, nh_;

  int linearx_,lineary_, angular_, deadman_axis_, turbo_axis_ , turbo_up_axis_, turbo_down_axis_;
  double l_scale_, a_scale_,l_turbo_maxscale_,l_turbo_scale_,a_turbo_maxscale_;
  ros::Publisher vel_pub_;
  ros::Subscriber joy_sub_;

  geometry_msgs::Twist last_published_;
  boost::mutex publish_mutex_;
  bool deadman_pressed_;
  bool turbo_pressed_;
  bool turbo_up_pressed_;
  bool turbo_down_pressed_;
  bool zero_twist_published_;
  ros::Timer timer_;
};

Omnijoy::Omnijoy():
  ph_("~"),
  linearx_(1),
  lineary_(2),
  angular_(0),
  deadman_axis_(4),
  turbo_axis_(5),
  turbo_up_axis_(6),
  turbo_down_axis_(7),
  l_scale_(0.1),
  a_scale_(0.2),
  l_turbo_scale_(0.2),
  l_turbo_maxscale_(0.4),
  a_turbo_maxscale_(0.4)
{
  ph_.param("axis_linear_x", linearx_, linearx_);
  ph_.param("axis_linear_y", lineary_, lineary_);
  ph_.param("axis_angular", angular_, angular_);
  ph_.param("axis_deadman", deadman_axis_, deadman_axis_);
  ph_.param("axis_turbo", turbo_axis_, turbo_axis_);
  ph_.param("axis_turbo_up", turbo_up_axis_, turbo_up_axis_);
  ph_.param("axis_turbo_down", turbo_down_axis_, turbo_down_axis_);
  ph_.param("scale_angular", a_scale_, a_scale_);
  ph_.param("scale_linear", l_scale_, l_scale_);
  ph_.param("turbo_scale_linear", l_turbo_scale_, l_turbo_scale_);
  ph_.param("turbo_max_scale_linear", l_turbo_maxscale_, l_turbo_maxscale_);
  ph_.param("turbo_scale_angular", a_turbo_maxscale_, a_turbo_maxscale_);


  deadman_pressed_ = false;
  turbo_pressed_ = false;
  turbo_up_pressed_ = false;
  turbo_down_pressed_ = false;
  zero_twist_published_ = false;

  vel_pub_ = ph_.advertise<geometry_msgs::Twist>("cmd_vel", 1, true);
  joy_sub_ = nh_.subscribe<sensor_msgs::Joy>("joy", 10, &Omnijoy::joyCallback, this);

  timer_ = nh_.createTimer(ros::Duration(0.1), boost::bind(&Omnijoy::publish, this));
}

void Omnijoy::joyCallback(const sensor_msgs::Joy::ConstPtr& joy)
{ 
  geometry_msgs::Twist vel;
  vel.angular.z = joy->axes[angular_];
  vel.linear.x = joy->axes[linearx_];
  vel.linear.y = joy->axes[lineary_];
  last_published_ = vel;
  deadman_pressed_ = joy->buttons[deadman_axis_];
  turbo_pressed_ = joy->buttons[turbo_axis_];
  turbo_up_pressed_ = joy->buttons[turbo_up_axis_];
  turbo_down_pressed_ = joy->buttons[turbo_down_axis_];

}

void Omnijoy::publish()
{
  boost::mutex::scoped_lock lock(publish_mutex_);
  if(turbo_up_pressed_ && !turbo_down_pressed_){
      l_turbo_scale_=l_turbo_scale_+0.05;
      if(l_turbo_scale_>l_turbo_maxscale_){
          l_turbo_scale_=l_turbo_maxscale_;
      }
  }
  if(!turbo_up_pressed_ && turbo_down_pressed_){
      l_turbo_scale_=l_turbo_scale_-0.05;
      if(l_turbo_scale_<l_scale_ ){
          l_turbo_scale_=l_scale_;
      }
  }

  if (deadman_pressed_ && !turbo_pressed_)
  {
    last_published_.linear.y=(last_published_.linear.y*l_scale_);
    last_published_.linear.x=last_published_.linear.x*l_scale_;
    last_published_.angular.z=last_published_.angular.z*a_scale_;
    vel_pub_.publish(last_published_);
    zero_twist_published_=false;
  }else if (deadman_pressed_ && turbo_pressed_)
  {
    last_published_.linear.y=(last_published_.linear.y*l_turbo_scale_);
    last_published_.linear.x=last_published_.linear.x*l_turbo_scale_;
    last_published_.angular.z=last_published_.angular.z*a_turbo_maxscale_;
    vel_pub_.publish(last_published_);
    zero_twist_published_=false;
  }
  else if(!deadman_pressed_ && !zero_twist_published_)
  {
    vel_pub_.publish(*new geometry_msgs::Twist());
    zero_twist_published_=true;
  }
}

} // namespace sdpo_driver_omnijoy

int main(int argc, char** argv)
{
  ros::init(argc, argv, "sdpo_driver_omnijoy");
  sdpo_driver_omnijoy::Omnijoy omni_joy;

  ros::spin();
}

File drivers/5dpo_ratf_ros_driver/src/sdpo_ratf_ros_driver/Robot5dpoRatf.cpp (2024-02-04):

#include "sdpo_ratf_ros_driver/Robot5dpoRatf.h"

#include <exception>
#include <utility>
#include <vector>

namespace sdpo_ratf_ros_driver {

const unsigned int kSerialBaudRate = 115200;
const auto kSerialDataBits = boost::asio::serial_port_base::character_size(8);
const auto kSerialStopBits = boost::asio::serial_port_base::stop_bits::one;
const auto kSerialParity = boost::asio::serial_port_base::parity::none;
const auto kSerialFlowCtrl = boost::asio::serial_port_base::flow_control::none;

void Motor::setEncoderRes(const double& enc_res) {
  if (enc_res <= 0) {
    throw std::invalid_argument(
        "[Robot5dpoRatf.cpp] Motor::setEncoderRes: "
        "resolution of the encoder must be greater than 0 (enc ticks / rev)");
  }
  encoder_res = enc_res;
}

void Motor::setGearReduction(const double& gear_ratio) {
  if (gear_ratio <= 0) {
    throw std::invalid_argument(
        "[Robot5dpoRatf.cpp] Motor::setGearReduction: "
        "gear reduction ratio of the motor must be greater than 0 ([n:1])");
  }
  gear_reduction = gear_ratio;
}

void Motor::setEncTicksDelta(const int32_t& delta_enc_ticks) {
  enc_ticks_delta = delta_enc_ticks;
  enc_ticks_delta_pub += enc_ticks_delta;
  enc_ticks_prev = enc_ticks;
  enc_ticks += enc_ticks_delta;
  setW();
}

void Motor::setEncTicks(const int32_t& total_enc_ticks) {
  enc_ticks_prev = enc_ticks;
  enc_ticks = total_enc_ticks;
  enc_ticks_delta = enc_ticks - enc_ticks_prev;
  enc_ticks_delta_pub += enc_ticks_delta;
  setW();
}

double Motor::getEncTicksDeltaPub() {
  double pub_delta = enc_ticks_delta_pub;
  enc_ticks_delta_pub = 0;
  return pub_delta;
}

void Motor::setPWM(const int16_t& pwm_mot) {
  if (pwm_mot > kMaxMotPWM) {
    pwm = kMaxMotPWM;
  } else if (pwm_mot < -kMaxMotPWM) {
    pwm = -kMaxMotPWM;
  } else {
    pwm = pwm_mot;
  }
}

void Motor::setWr(const double& w_ref) {
  w_r = w_ref;
}

void Motor::setSampleTime(const int32_t& time_sample) {
  sample_time_prev = sample_time;
  sample_time = static_cast<double>(((float) time_sample) / 1.0e6); // us > s
  sample_period = sample_time - sample_time_prev;
}

void Motor::reset() {
  enc_ticks = 0;
  enc_ticks_prev = 0;
  enc_ticks_delta = 0;
  enc_ticks_delta_pub = 0;
  pwm = 0;
  w_r = 0;
  w = 0;
  sample_time = 0;
  sample_time_prev = 0;
  sample_period = 0;
}

void Motor::setW() {
  w = 2 * M_PI * enc_ticks_delta * kMotCtrlFreq /
      (gear_reduction * encoder_res);
}

Robot5dpoRatf::Robot5dpoRatf() : serial_async_(nullptr) {
  serial_cfg_ = InitCommunications();
}

Robot5dpoRatf::Robot5dpoRatf(std::string serial_port_name)
    : serial_async_(nullptr),
      serial_port_name_(std::move(serial_port_name)) {
  serial_cfg_ = InitCommunications();
}

Robot5dpoRatf::~Robot5dpoRatf() {
  closeSerial();
}

void Robot5dpoRatf::init() {
  reset();
  if (isSerialOpen()) {
    sendSerialData();
  }
}

bool Robot5dpoRatf::openSerial(const bool dbg) {
  try {
    serial_async_ = new CallbackAsyncSerial(
        serial_port_name_, kSerialBaudRate,
        boost::asio::serial_port_base::parity(kSerialParity),
        kSerialDataBits,
        boost::asio::serial_port_base::flow_control(kSerialFlowCtrl),
        boost::asio::serial_port_base::stop_bits(kSerialStopBits));
    serial_async_->setCallback(
        std::bind(&Robot5dpoRatf::rcvSerialData, this,
                  std::placeholders::_1, std::placeholders::_2));
    return true;
  } catch (boost::system::system_error& e) {
    serial_async_ = nullptr;
    if (dbg) {
      std::cerr << "[Robot5dpoRatf.cpp] Robot5dpoRatf::openSerial: "
                   "Error when opening the serial device "
                << serial_port_name_ << std::endl;
    }
    return false;
  }
}

void Robot5dpoRatf::closeSerial(const bool dbg) {
  if (serial_async_) {
    try {
      serial_async_->close();
    } catch(...) {
      if (dbg) {
        std::cerr << "[Robot5dpoRatf.cpp] Robot5dpoRatf::closeSerial: "
                     "Error when closing the serial device "
                  << serial_port_name_ << std::endl;
      }
    }
    delete serial_async_;
  }
}

bool Robot5dpoRatf::isSerialOpen() {
  return serial_async_ ?
         !(serial_async_->errorStatus() || (!serial_async_->isOpen())) : false;
}

void Robot5dpoRatf::setSerialPortName(const std::string& serial_port_name) {
  serial_port_name_ = serial_port_name;
}

void Robot5dpoRatf::reset() {
  for(auto& m : mot) {
    m.reset();
  }
}

void Robot5dpoRatf::stopMotors() {
  for(auto& m : mot) {
    m.w_r = 0;
  }
}

void Robot5dpoRatf::rcvSerialData(const char *data, unsigned int len) {
  std::vector<char> vec(data, data + len);
  char channel;

  for(auto& c : vec) {
    if (!((c < 32) || (c >= 0x7f))) { // ignore non-ascii char
      channel = ProcessChannelsSerialData(c);

      if (channel > 0) {
        switch (channel) {
        case 'g':
          sendSerialData();
          if (run) {
            run();
          }
          mtx_.lock();
          mot[0].setEncTicks(serial_cfg_->channel_g);
          mtx_.unlock();
          break;

        case 'h':
          mtx_.lock();
          mot[1].setEncTicks(serial_cfg_->channel_h);
          mtx_.unlock();
          break;

        case 'i':
          mtx_.lock();
          mot[2].setEncTicks(serial_cfg_->channel_i);
          mtx_.unlock();
          break;

        case 'j':
          mtx_.lock();
          mot[3].setEncTicks(serial_cfg_->channel_j);
          mtx_.unlock();
          break;

        case 'k':
          mtx_.lock();
          for(auto& m : mot) {
            m.setSampleTime(serial_cfg_->channel_k);
          }
          mtx_.unlock();
          break;

        case 'r':
          mtx_.lock();
          reset();
          mtx_.unlock();
          break;

        case 's':
          mtx_.lock();
          switch_state = (serial_cfg_->channel_s == 0);
          mtx_.unlock();

        default:
          break;
        }
      }
    }
  }
}

void Robot5dpoRatf::sendSerialData() {
  mtx_.lock();
  serial_cfg_->channel_G = static_cast<float>(mot[0].w_r);
  serial_cfg_->channel_H = static_cast<float>(mot[1].w_r);
  serial_cfg_->channel_I = static_cast<float>(mot[2].w_r);
  serial_cfg_->channel_J = static_cast<float>(mot[3].w_r);
  serial_cfg_->channel_L = solenoid_state? 1 : 0;
  mtx_.unlock();

  serial_async_->writeString(SendChannel('G'));
  serial_async_->writeString(SendChannel('H'));
  serial_async_->writeString(SendChannel('I'));
  serial_async_->writeString(SendChannel('J'));
  serial_async_->writeString(SendChannel('L'));
}

} // namespace sdpo_ratf_ros_driver

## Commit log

2024-02-04 System Framework for R@F developed by 5dpo
    [log_tune_batt-11.73_2023-04-25-19-03-44.csv, log_tune_batt-11.75_2023-04-25-18-58-34.csv, log_tune_batt-11.79_2023-04-25-18-47-34.csv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]
2024-02-04 Add IMU support + scaling of wheel angular speed
    [ImuFilterMadgwick.cfg]
2024-02-04 3D STEP files
    [Anilha.stp, Anilha_4.stp, Cam+V2.stp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]
2024-02-10 Add missing HMI node
    [main.cpp]
